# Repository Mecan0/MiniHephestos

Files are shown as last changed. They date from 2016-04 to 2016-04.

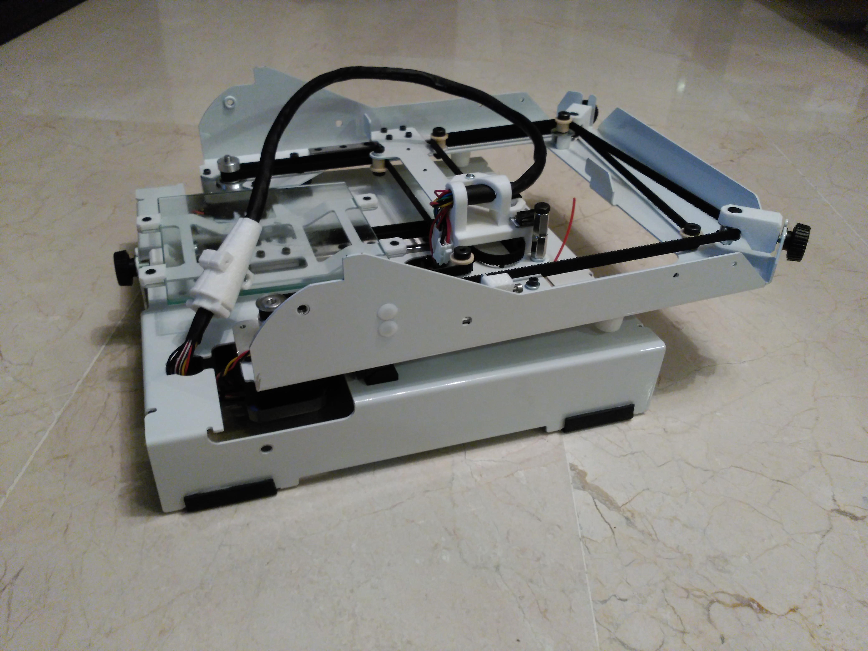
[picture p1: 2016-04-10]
03 The Hephestos Mini Printer.jpg

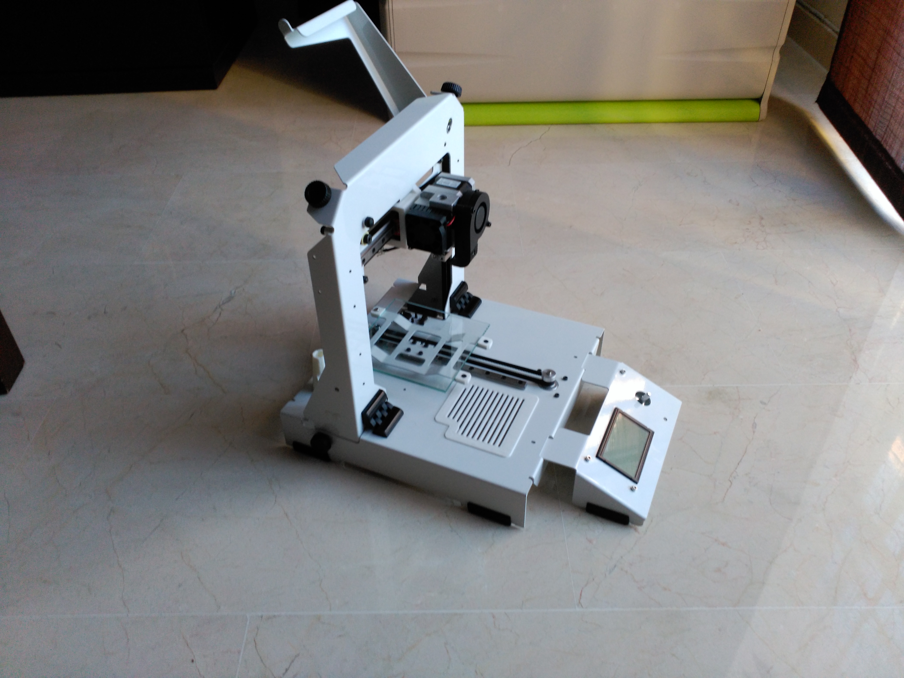
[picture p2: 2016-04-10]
02 The Hephestos Mini Printer.jpg

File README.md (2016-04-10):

# Hephestos-Mini
Mini 3D printer foldable

La Hephestos Mini nace como una colaboración entre BQ y Manuel Palacios para crear una impresora pequeña y transportable de fácil montaje.
El diseño está pensado para fabricarlo con chapa cortada por laser y posteriormente plegada.
Se ha tratado de minimizar el número de piezas diferentes para simplificar el montaje al máximo.
Los materiales utilizados para el diseño han sido los que integra BQ en sus impresoras, electrónica, extrusor, finales de carrera... 
Aunque es fácil modificarlo para adaptarlo a otros materiales.
El firmware elegido es de Repetier porque tiene un módulo para Core XZ, en Marlin existen otras versiones pero no están tan depurados.

Siente te libre de usar, modificar o adaptarlo a tu gusto.

A pioner in Core XZ printers is Nicholas Seward, Thanks a lot

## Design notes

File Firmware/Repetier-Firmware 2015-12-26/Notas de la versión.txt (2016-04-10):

Este firmware está basado en la versión 0.92.3

Tiene la corrección de Repetier que se muestra en el foro siguiente hecha maualmente

http://forums.reprap.org/read.php?267,392590,page=2 

Aunque a partir de la versión 0.92.6 esta corrección venía de serie.

Para funcionar con la Zum Mega 3D
En el archivo pins.h tiene cambiado:

#define ORIG_Z_ENABLE_PIN       77 //62

#define ORIG_FAN_PIN            12 //9
#define ORIG_PS_ON_PIN          81 //12

#define HEATER_0_PIN       9 //10
#define HEATER_1_PIN       10 //8
#define HEATER_2_PIN       8 //9

Una vez que se mete el firmware es necesario cargar los valores de la EEprom importando el archivo
 EEpromParaImprimir.epr desde Repetier Host.
 
 1) Conectar la impresora
 
 2) Menu Configuración\Config firmware EEPROM -----> Import EEPROM

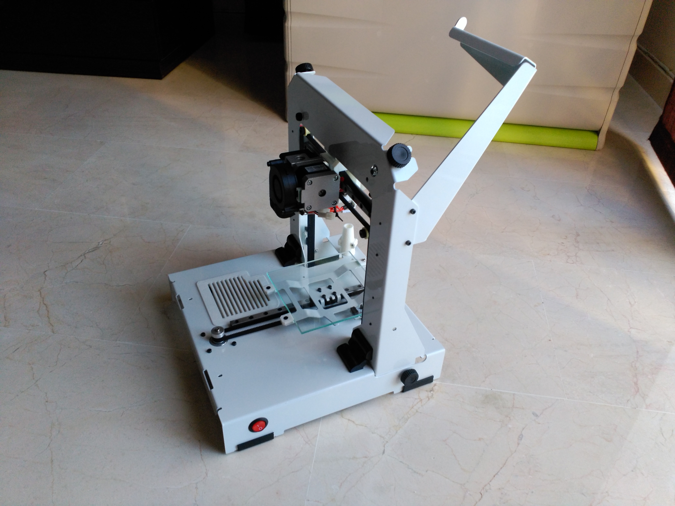
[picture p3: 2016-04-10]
Photos/2015-11-29 10.03.52.jpg

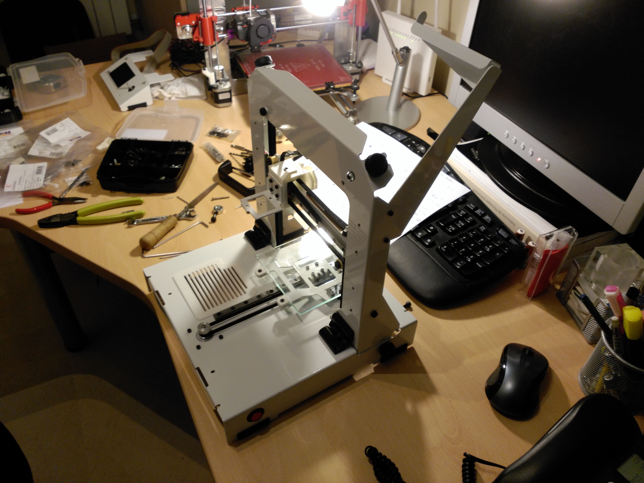
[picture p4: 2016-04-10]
Photos/2015-11-28 19.54.12.jpg

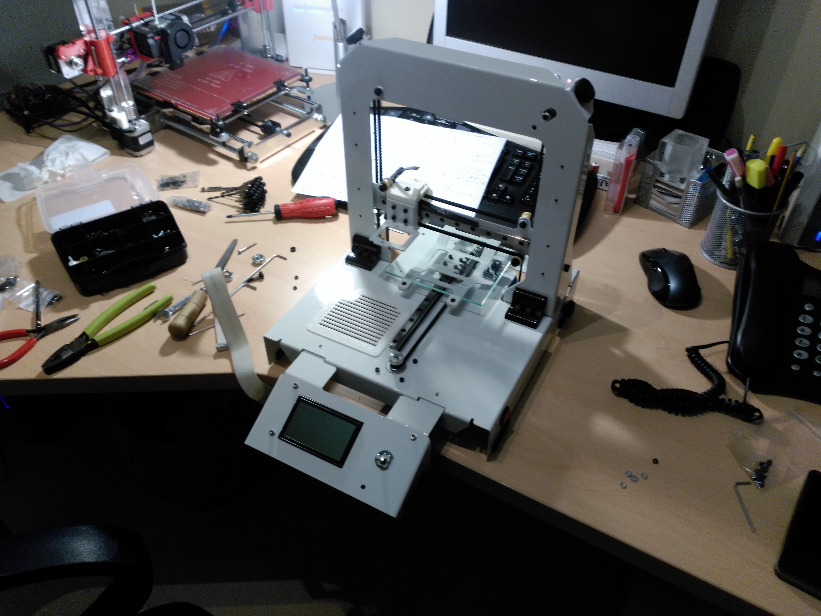
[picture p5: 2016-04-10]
Photos/2015-11-28 19.30.46.jpg

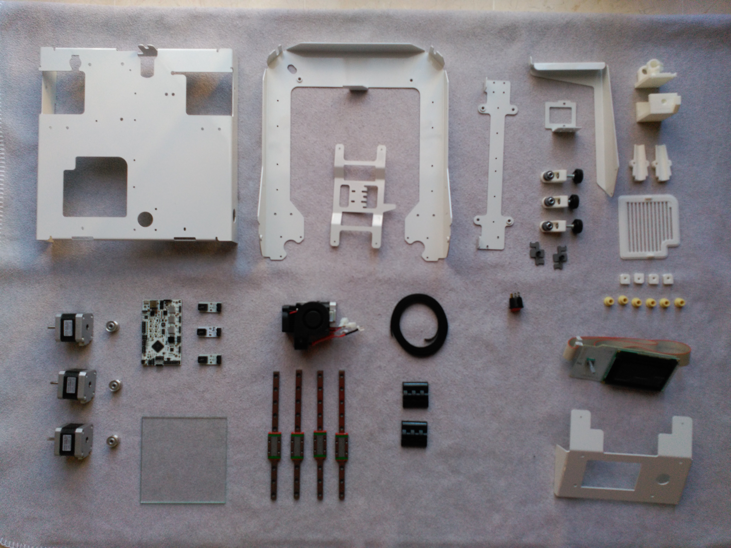
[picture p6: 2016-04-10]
04 Pieces.jpg

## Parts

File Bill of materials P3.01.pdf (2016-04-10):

REF | Nombre | Material | Unidades | Imagen

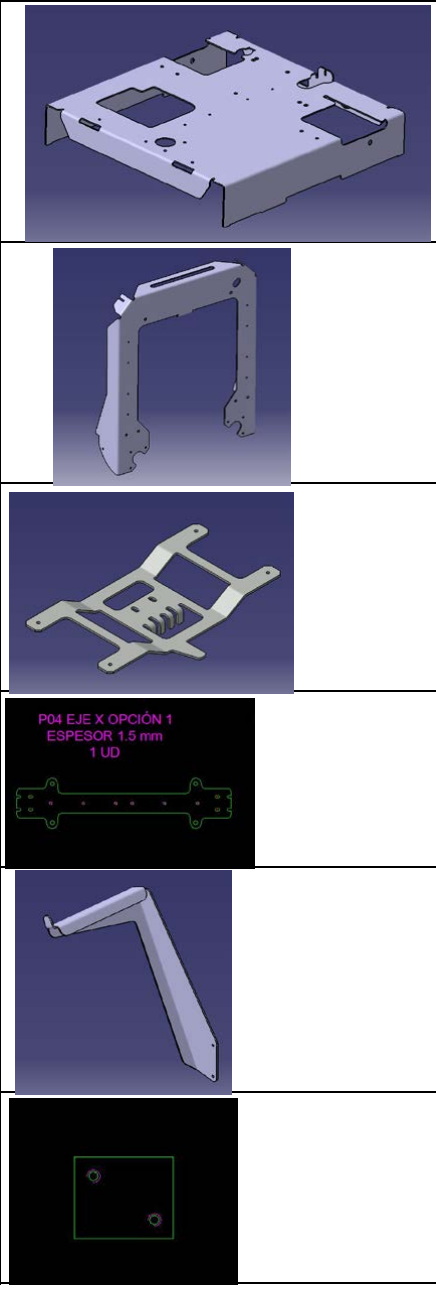
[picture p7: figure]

P01 | Base | | 1
P02 | Arco | | 1
P03 | Plataforma | | 1
P04 | Eje X | | 1
P05 | ReelH | | 1
P06 | FijCorrea | | 2

Metal

Metal

Metal

Metal

Metal

Metal

# BILL OF MATERIALS

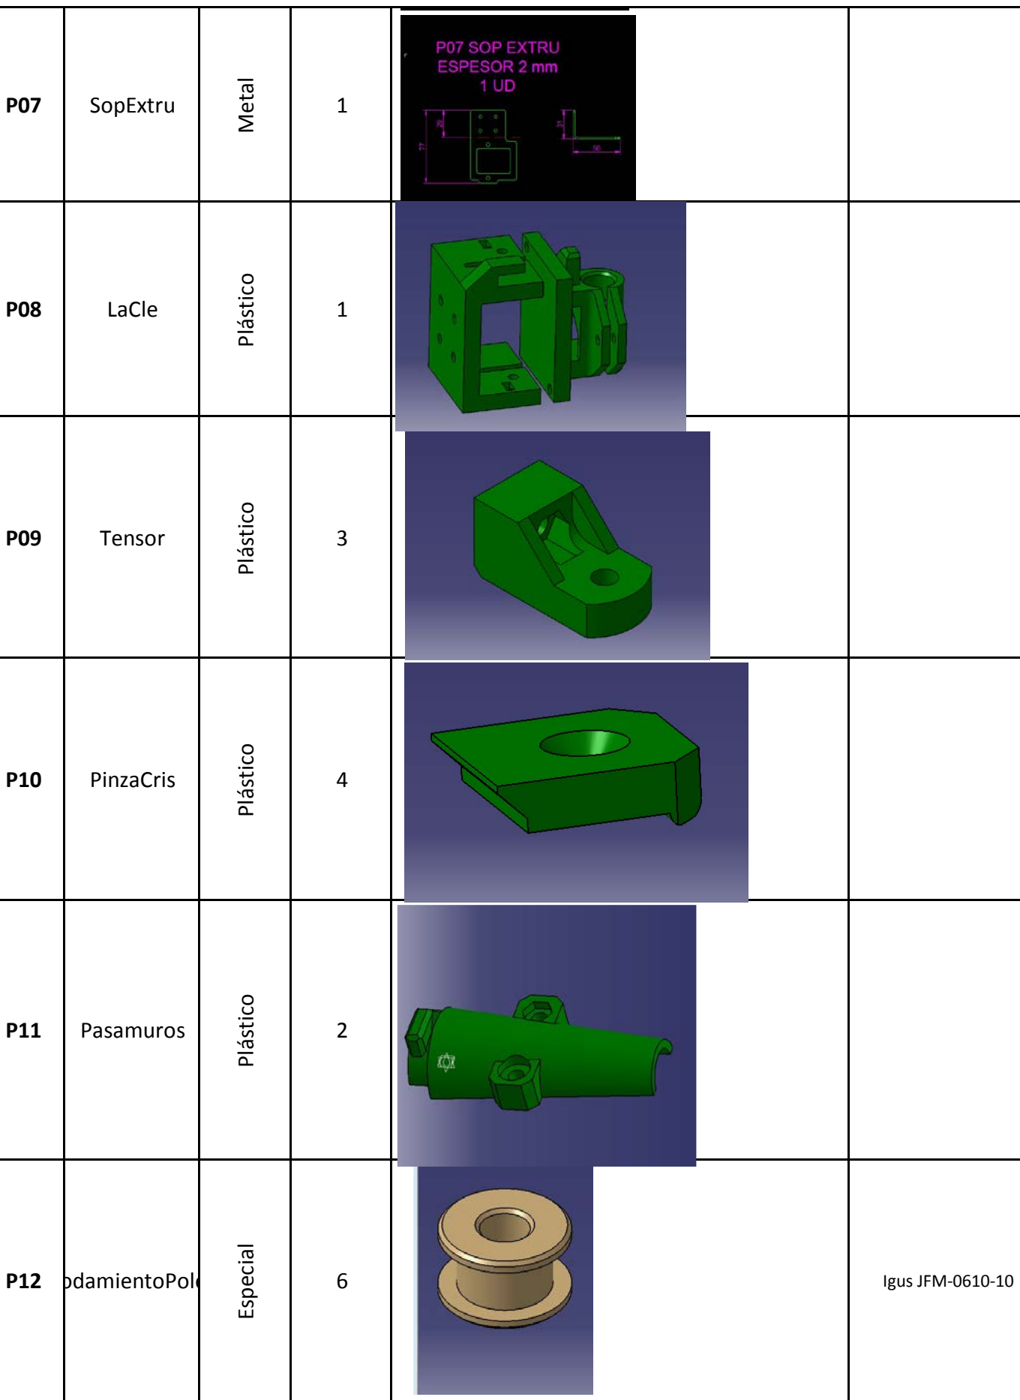
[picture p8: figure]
Metal; Plástico; P12 odamientoPole; Igus JFM-0610-10; Especial

P07 | SopExtru | 1
P08 | LaCle | 1
P09 | Tensor | 3
P10 | PinzaCris | 4
P11 | Pasamuros | 2

P13 | Rejilla | 1

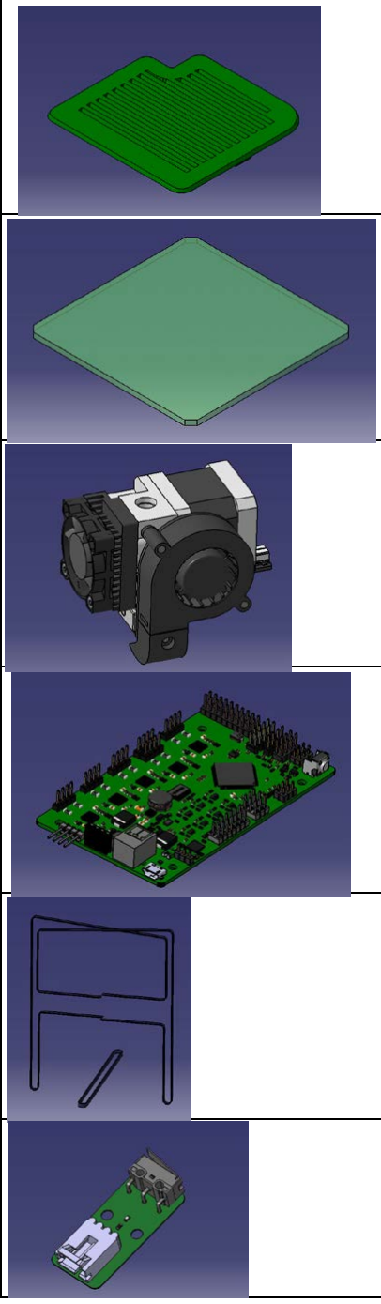
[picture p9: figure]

P14 | Cristal | 1 | Dimensiones 130 x 130 x 4 , perímetro biselado 1 x 45º
P15 | Extrusor | 1
P16 | Electrónica | 1
P17 | Correas | 1 | Correa eje Y 550 mm, Correas XZ 2 ud a 980 para después recortar
P18 | Fcarrera | 3

## Plástico

## Especial

## Comercial

## Comercial

## Comercial

## Comercial

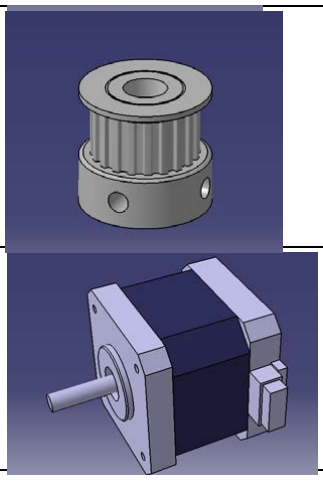
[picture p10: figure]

P19 | PoleaGT2 | 3
P20 | Motores | 3
P21 | 685ZZ | 3 | Rodamiento diam ext 11 mm, eje 5 mm y anchura 5 mm.
P22 | Bisagra | 2

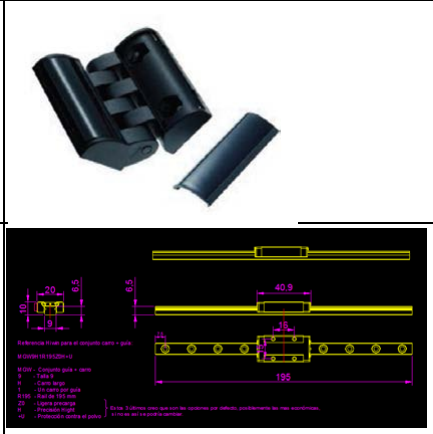
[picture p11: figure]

P23 | G_HIWIN | 4 | | Referencia Hiwin para el conjunto carro + guía: MGN9H1R195Z0H+U MGN - Serie MGN 9 - Talla 9 H - Carro largo 1 - Un carro por guía R195 - Rail de 195 mm Z0 - Ligera precarga H - Precisión Hight +U - Protección contra el polvo

## Comercial

## Comercial

## Comercial

## Comercial

## Comercial

## OPCIONAL

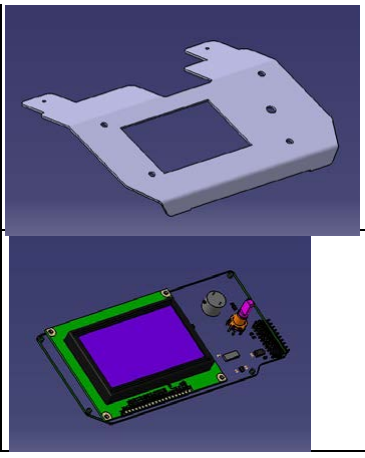
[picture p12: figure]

## P30 SopLCD

## Metálico

1

## P31 LCD

## Comercial

1

Tornillería | | Para: | Cantidad
Tornillo DIN912 M3x5 | Cabeza Allen | Para motores | 9 ud
Tornillo DIN912 M3x5 | Cabeza Allen | Para fijar guías y rollo y caros Z | 25 ud
Tornillo DIN912 M4x8 | Cabeza Allen | Para Bisagras y cogida correas | 10 ud
Tornillo DIN7379 M5x6x12 | Cabeza Allen | Tornillos tope guía | 6 ud | Longitud parte diam 6
Tuercas M4 DIN934 | | Dentro bisagras | 8 ud
Tuercas M5 DIN934 | | Tensores y Calzo Correa | 7 ud
Tuercas M5 autoblocantes | | Tensores | 3 ud
Arandelas DIN125 M4 estandar | | Bisagras | 8 ud | No las usé
Arandelas DIN125 M5 estándar | | Tensores | 9 ud
Arandelas DIN9021 M5 vuelo | | Tensores | 6 ud
Tornillo DIN933 M5x20 | Cabeza hexagonal | Tensores y final de carrera X | 4 ud
Tornillo DIN912 M3x20 | Cabeza Allen | Tope FCZ | 1 ud
Tuercas M3 DIN 934 | Cabeza Allen | Tope final de Carrera Z y carros Z | 9 ud
Tuerca larga de M5 DIN6334 | | Tope final de carrera X | 2 ud
Tuerca M10 Din 934 | | Suplemento polea | 2 ud
Tornillo DIN 912 M3x5 | Cabeza Allen | Union Plataf-carro y EjeX-Carro | 12 ud
Tornillo DIN 945 M3x8 | Cabeza cónica Allen | Pinzas Cristal | 4 ud
Tornillo DIN 912 M3x10 | Cabeza Allen | fijac electrónica, Carros Z | 8 ud
Tornillo DIN 912 M3x12 | Cabeza Allen | Union SopExtr-Carro | 4 ud
Tornillo para plástico 3x10 | Wurth Ref: 42 16 3 10 | Tapa Cle, Pasamuros y Fijación Cable | 6 ud
Tornillo apriete manual M5x10 | Essentra Ref: KTSR-23M05M10 Fijación a 90º | 2 ud | Lo ideal sería que tubi
http://www.essentracomponents.es/pomos-de-agarre-344390
Tornillo aprete manual M5x20 | Essentra Ref: KTSR-23M05M20 Tensores | 3 ud | En Essentra tienen de
| Ver también Essentra Ref.: 466347

Essentra

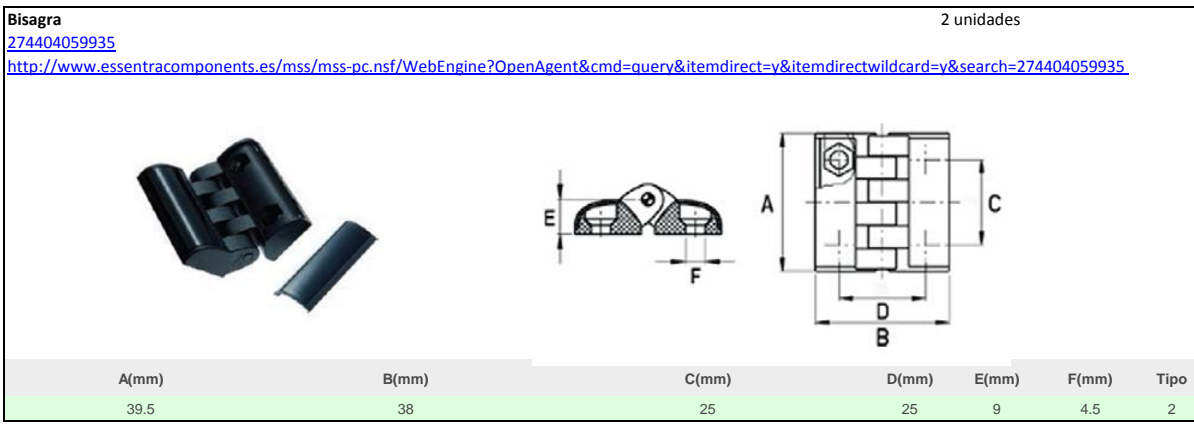
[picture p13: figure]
Bisagra; 2 unidades; 274404059935 http://www.essentracomponents.es/mss/mss-pc.nsf/WebEngine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; Tipo

Cantidad nec.

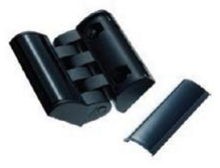
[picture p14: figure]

Separador electrónica, finales de carrera.
RLCBSR-5-01BK (http://www.essentracomponents.es/mss/mss-pc.nsf/WebEngine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) | Para final de carrera Z | Altura de parada 7,9 mm | 5 | Ver cogida LCD
RLCBSPR-4-01 (http://www.essentracomponents.es/mss/mss-pc.nsf/WebEngine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) | Para final de carrera Y | Altura de parada 6,4 | 2
http://www.essentracomponents.es/separador-circuito-impreso-con-base-de-remache---rlcbsrrlcbsrerlcbsprrcbsr
Esta referencia es en color negro, también existe en blanco. Tipo 1 Con Gancho.


Patas | RG-1 | 4 ud x 50mm
http://www.essentracomponents.es/mss/mss-pc.nsf/WebEngine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


Otra opción para las patas mas económica pero mucho mas fea: 492988S

http://www.essentracomponents.es/protector-de-bordes-de-pvc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


4 ud x 50mm
| Dependerá del precio y de las muestras

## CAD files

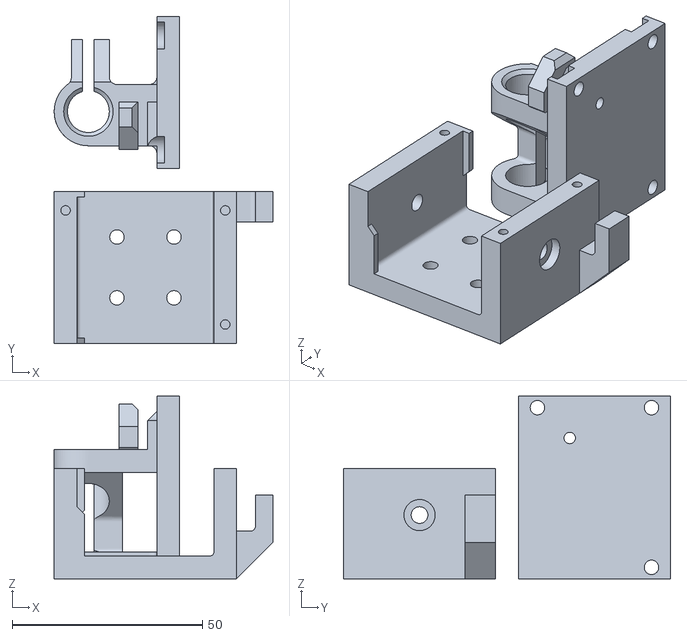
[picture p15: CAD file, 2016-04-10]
STL Files/P08_LaCle.stl
57.5 x 86.0 x 48.0

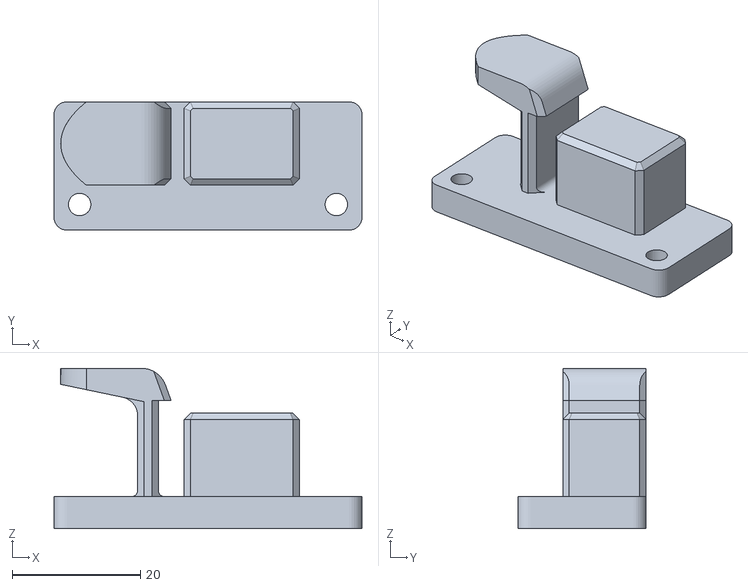
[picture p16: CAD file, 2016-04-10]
STL Files/P23_Cierre.stl
48.0 x 20.0 x 25.0

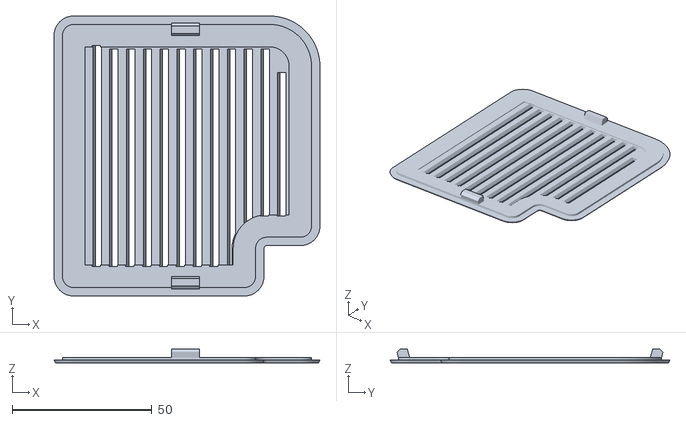
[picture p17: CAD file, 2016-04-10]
STL Files/P13_Rejilla.stl
95.0 x 100.0 x 5.00

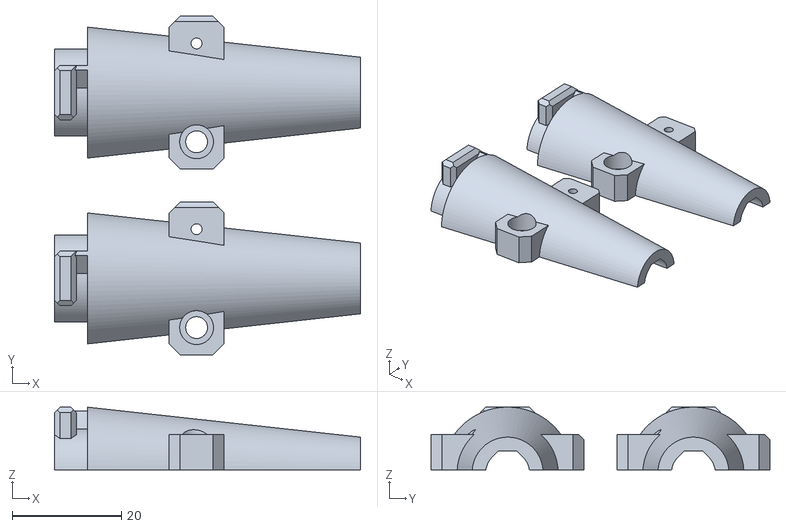
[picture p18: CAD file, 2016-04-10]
STL Files/P11_Pasamuros.stl
56.0 x 62.0 x 11.5

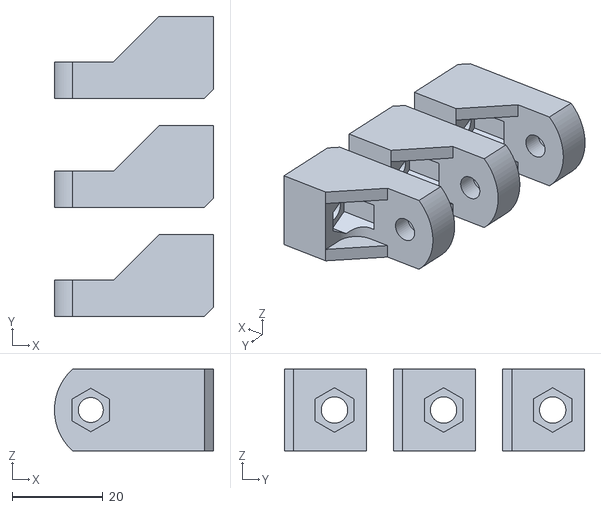
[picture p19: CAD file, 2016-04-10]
STL Files/P09_TensorV3.stl
35.0 x 66.0 x 18.0

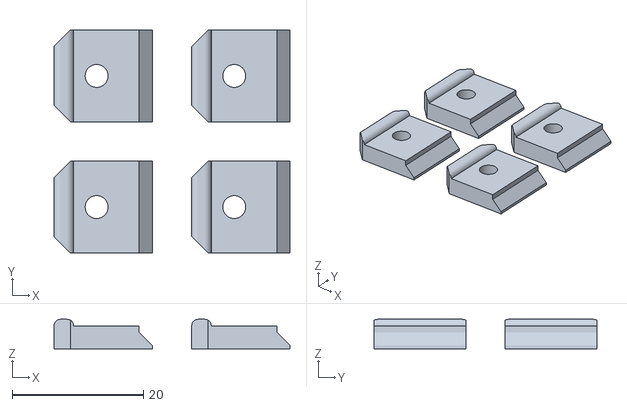
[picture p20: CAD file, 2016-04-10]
STL Files/P10_PinzaCris.stl
36.0 x 34.0 x 4.50

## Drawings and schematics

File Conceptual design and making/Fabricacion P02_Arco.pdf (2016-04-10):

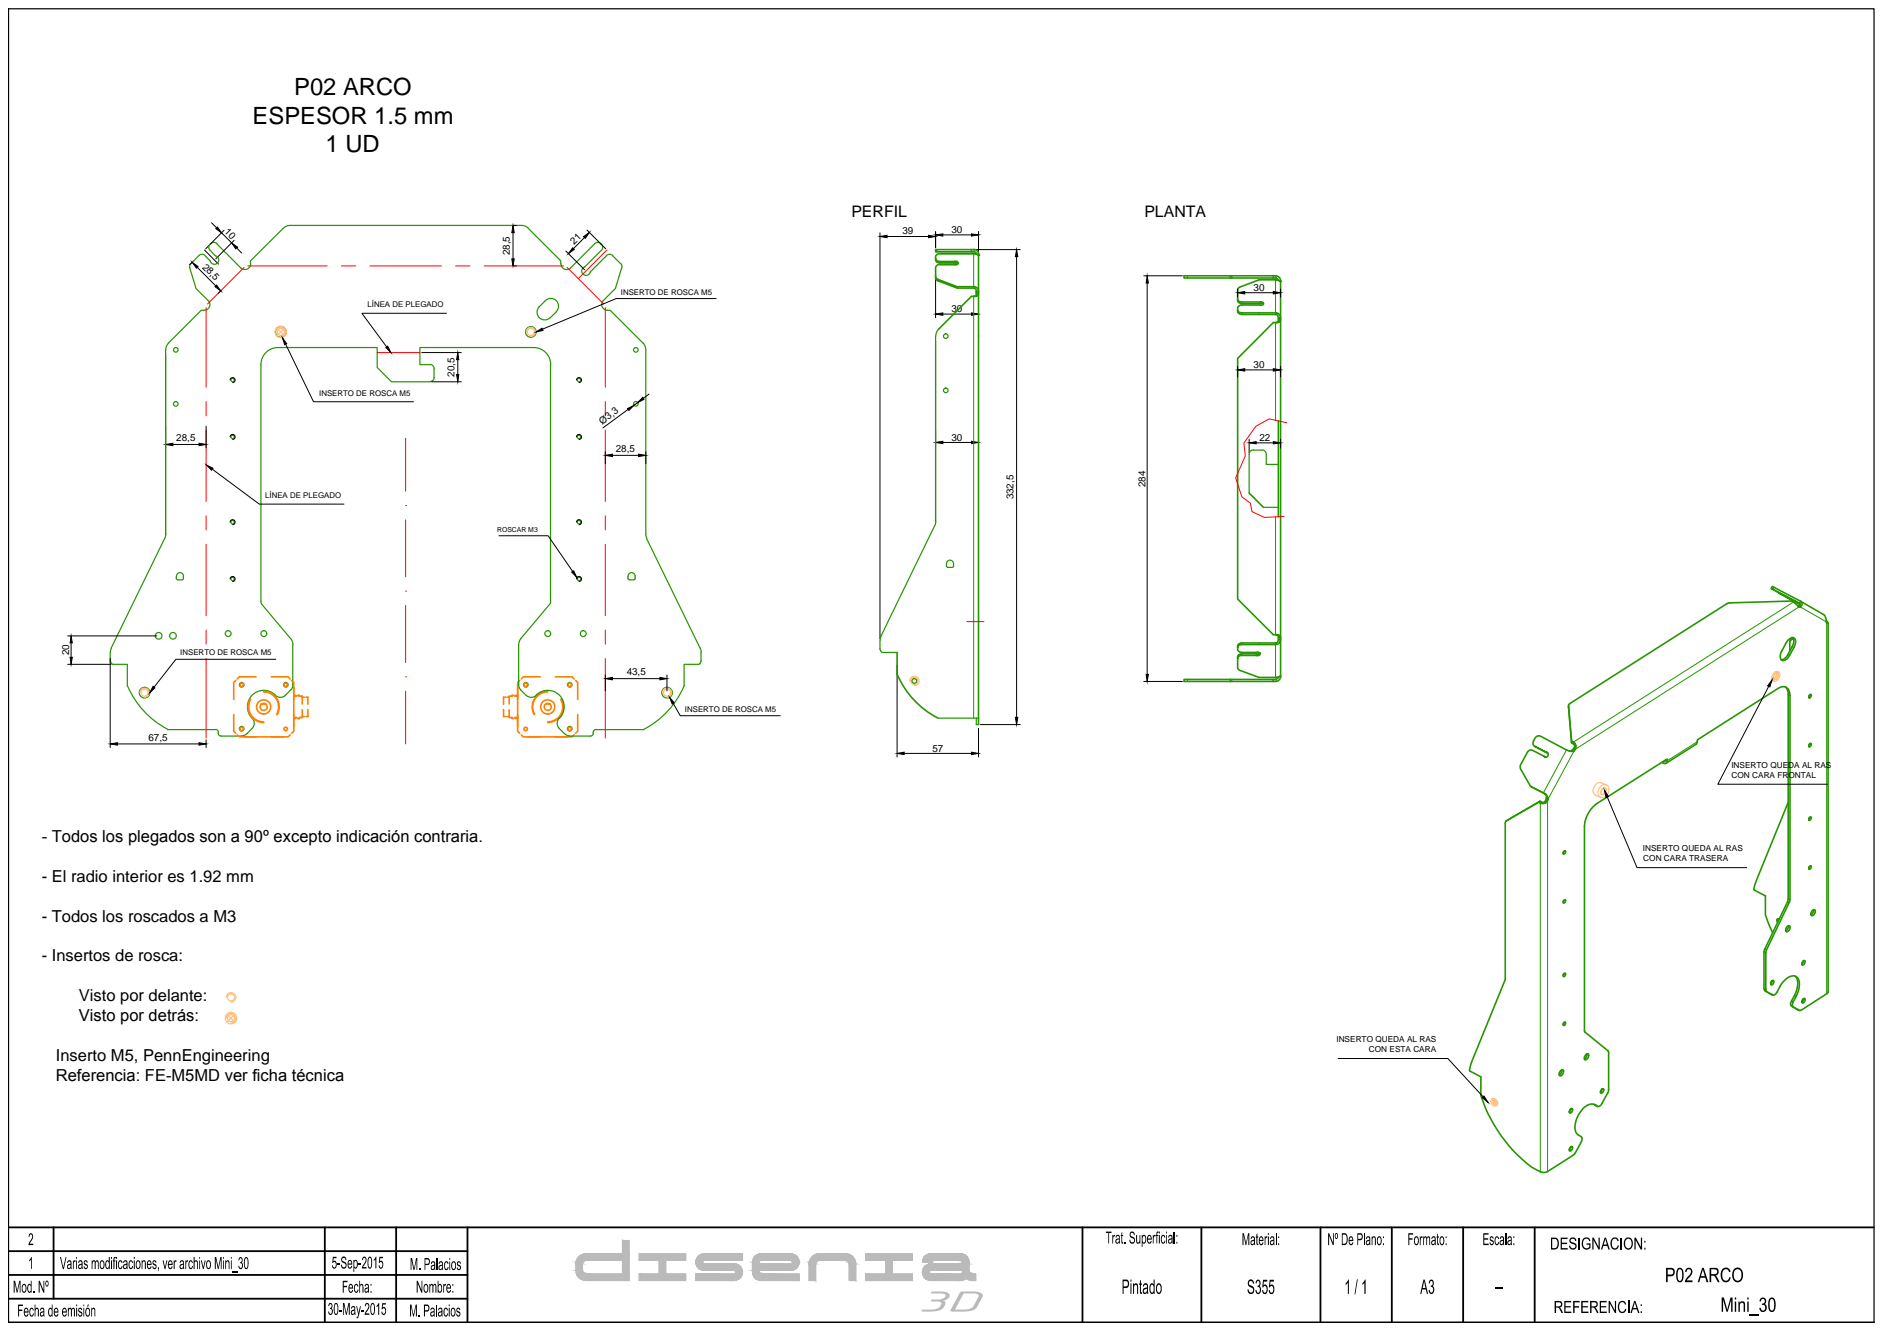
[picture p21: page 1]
P02 ARCO ESPESOR 1.5 mm 1 UD; ROSCAR M3

INSERTO DE ROSCA M5

INSERTO QUEDA AL RAS CON CARA FRONTAL

7RGRVORVSOHJDGRVVRQDH[FHSWRLQGLFDFLyQFRQWUDULD

INSERTO QUEDA AL RAS CON CARA TRASERA

- El radio interior es 1.92 mm

- Todos los roscados a M3

- Insertos de rosca:

Visto por delante:
9LVWRSRUGHWUiV

INSERTO QUEDA AL RAS CON ESTA CARA

Inserto M5, PennEngineering
5HIHUHQFLD)(00'YHUILFKDWpFQLFD

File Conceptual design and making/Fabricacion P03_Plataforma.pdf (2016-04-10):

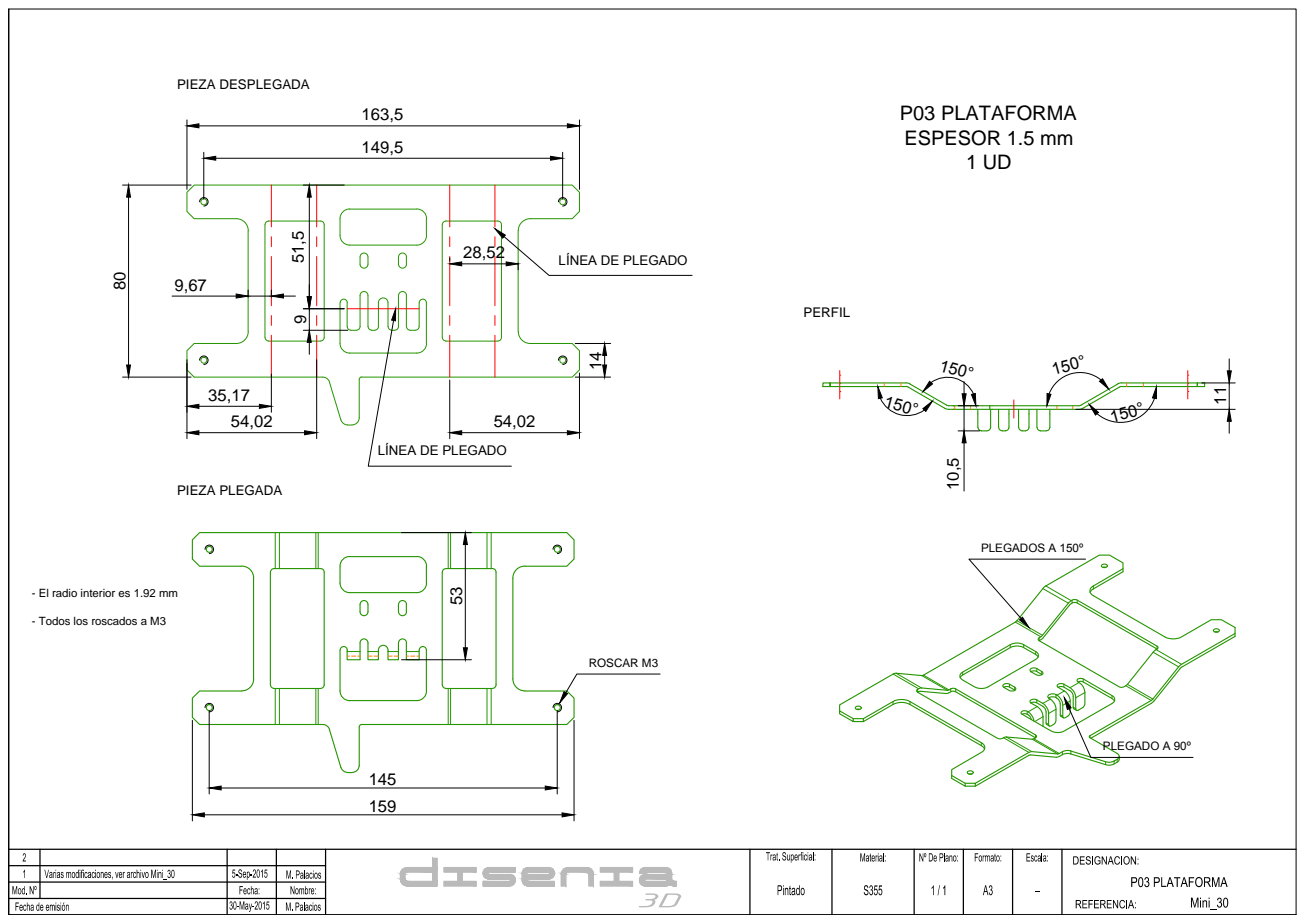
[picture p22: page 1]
P03 PLATAFORMA ESPESOR 1.5 mm 1 UD; PIEZA DESPLEGADA; PIEZA PLEGADA; ROSCAR M3

- El radio interior es 1.92 mm

- Todos los roscados a M3

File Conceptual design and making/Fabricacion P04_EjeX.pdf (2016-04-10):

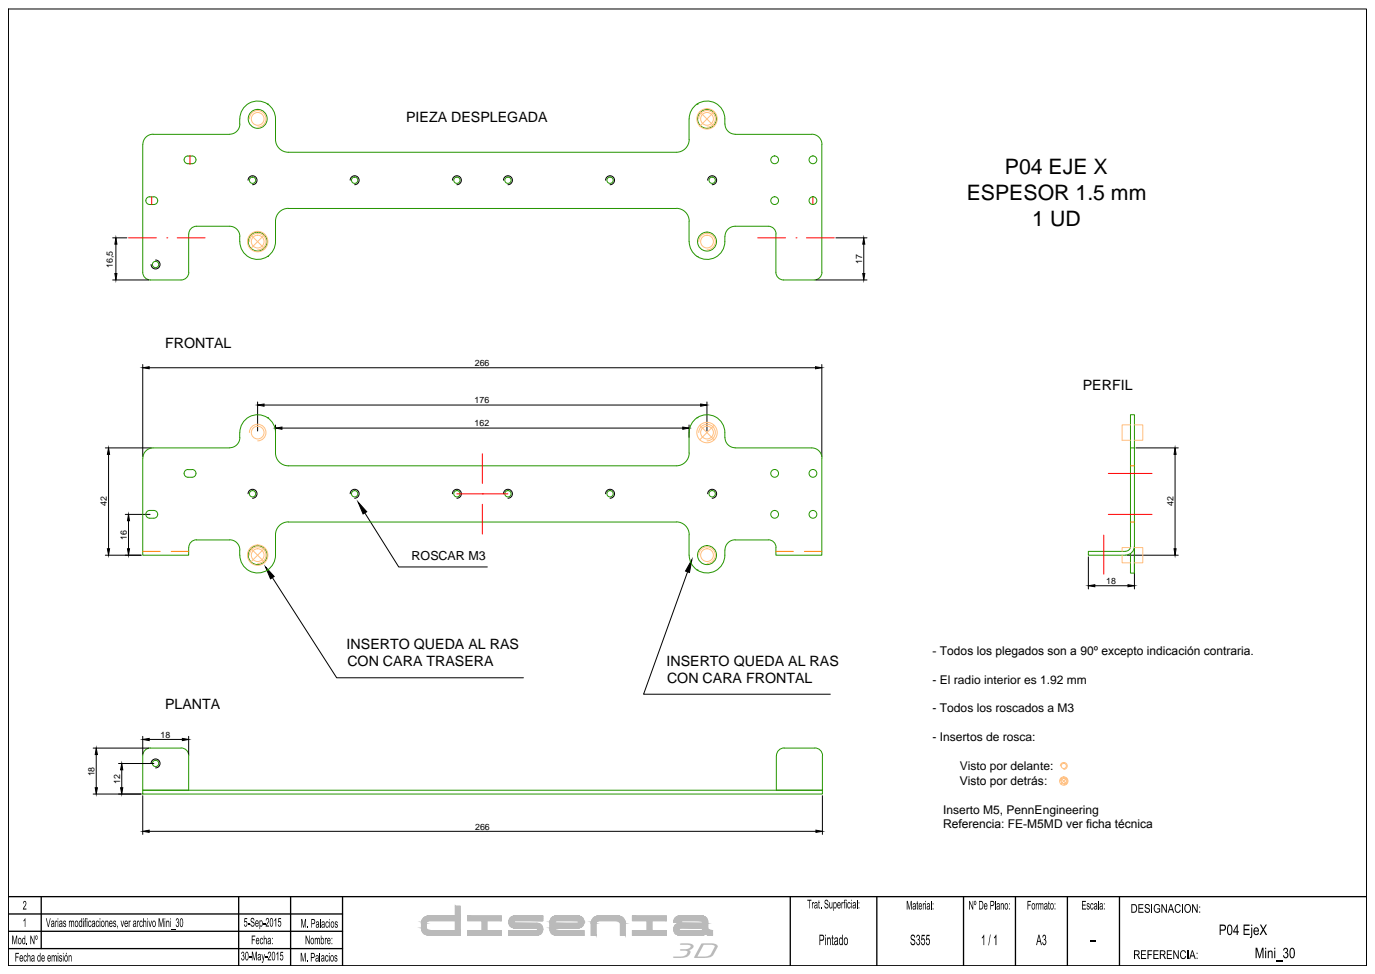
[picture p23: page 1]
P04 EJE X ESPESOR 1.5 mm 1 UD; ROSCAR M3; PIEZA DESPLEGADA

INSERTO QUEDA AL RAS
CON CARA TRASERA

7RGRVORVSOHJDGRVVRQDH[FHSWRLQGLFDFLyQFRQWUDULD

CON CARA FRONTAL

- El radio interior es 1.92 mm

- Todos los roscados a M3

- Insertos de rosca:

Visto por delante:
9LVWRSRUGHWUiV

Inserto M5, PennEngineering
5HIHUHQFLD)(00'YHUILFKDWpFQLFD

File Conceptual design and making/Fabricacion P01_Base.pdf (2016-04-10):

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

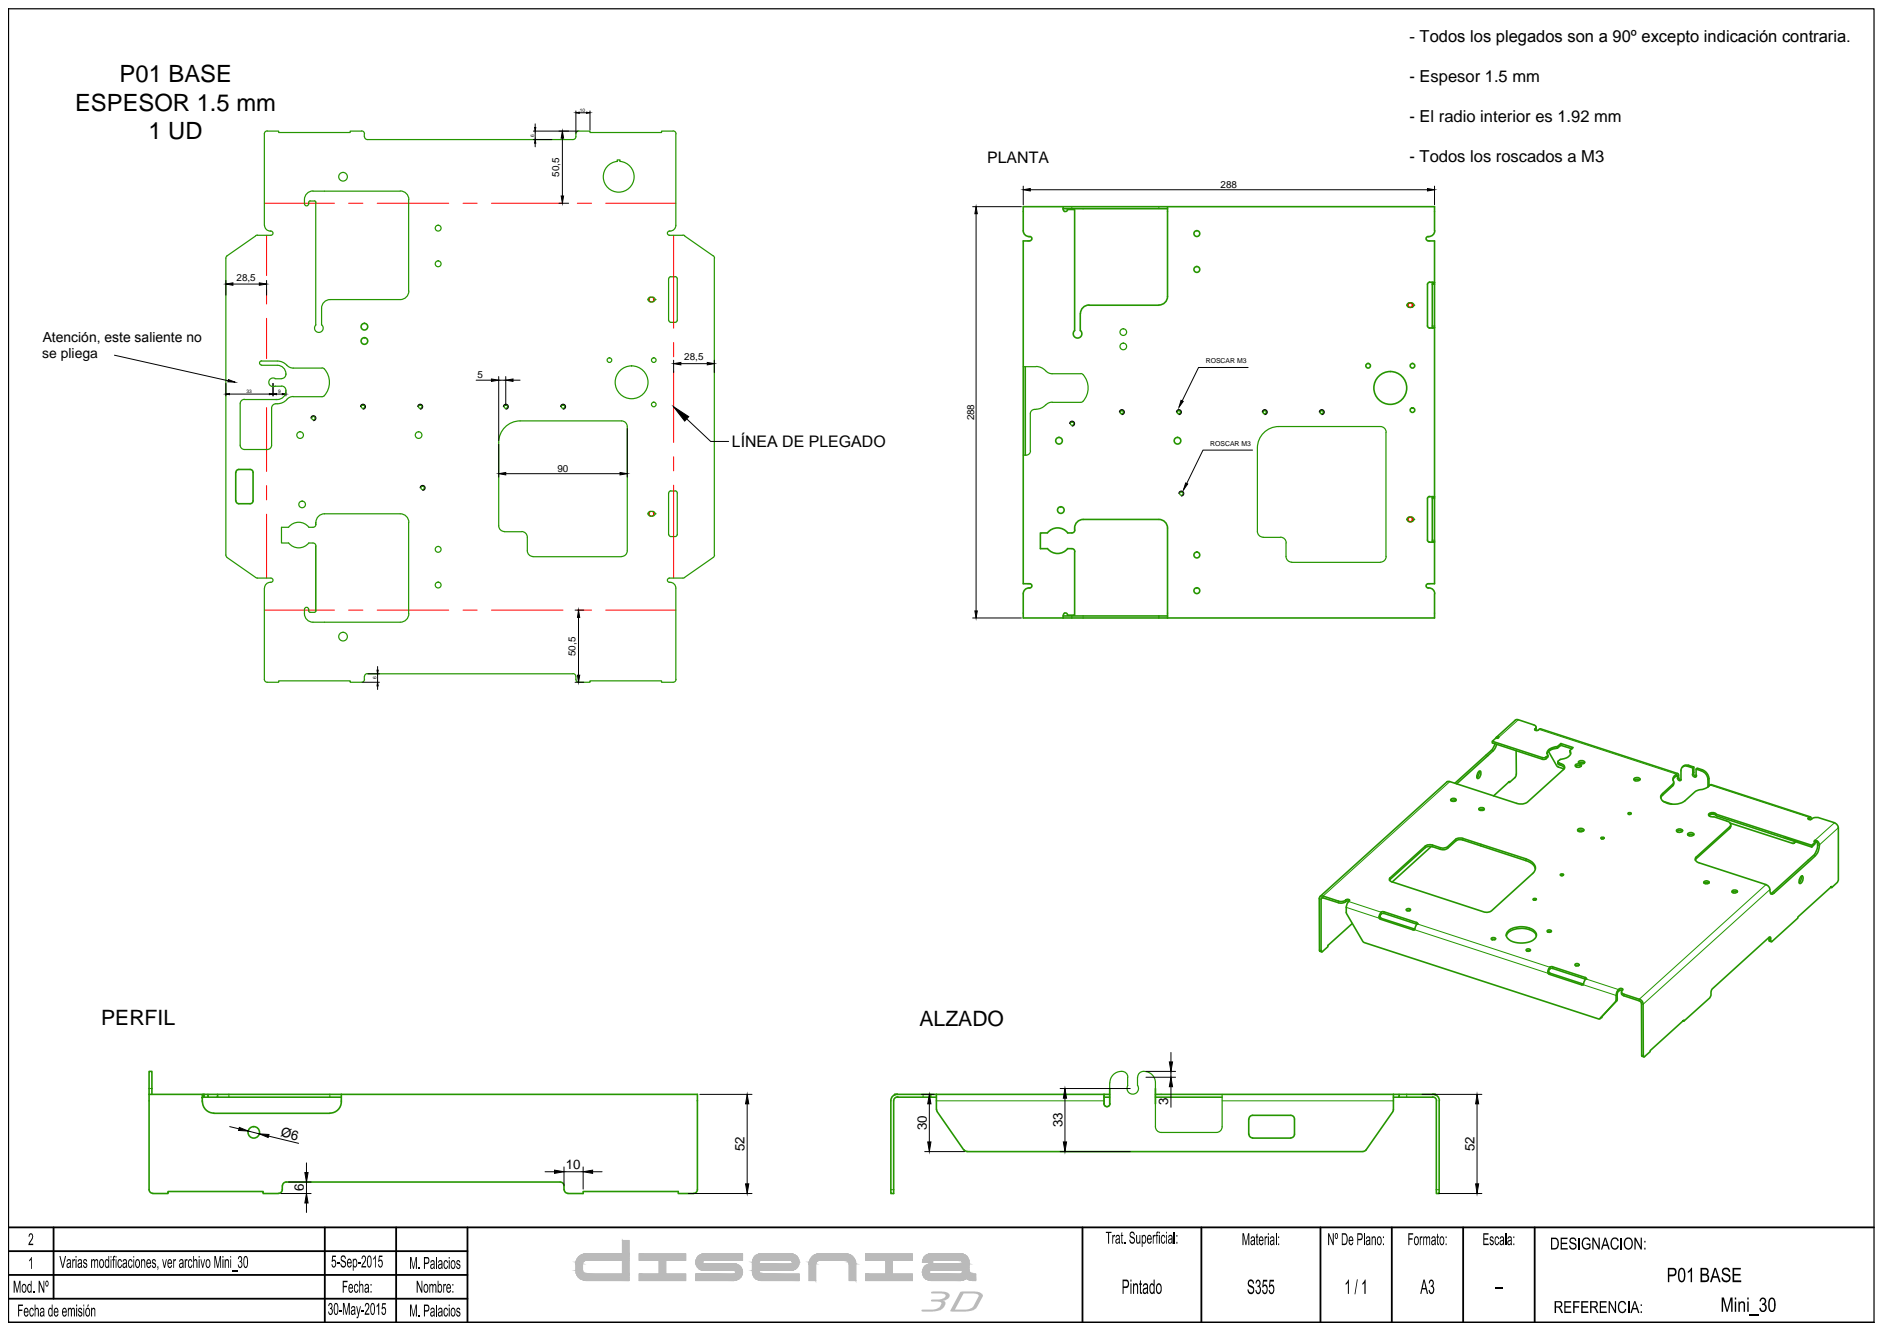
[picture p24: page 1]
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

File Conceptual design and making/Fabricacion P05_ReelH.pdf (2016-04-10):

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

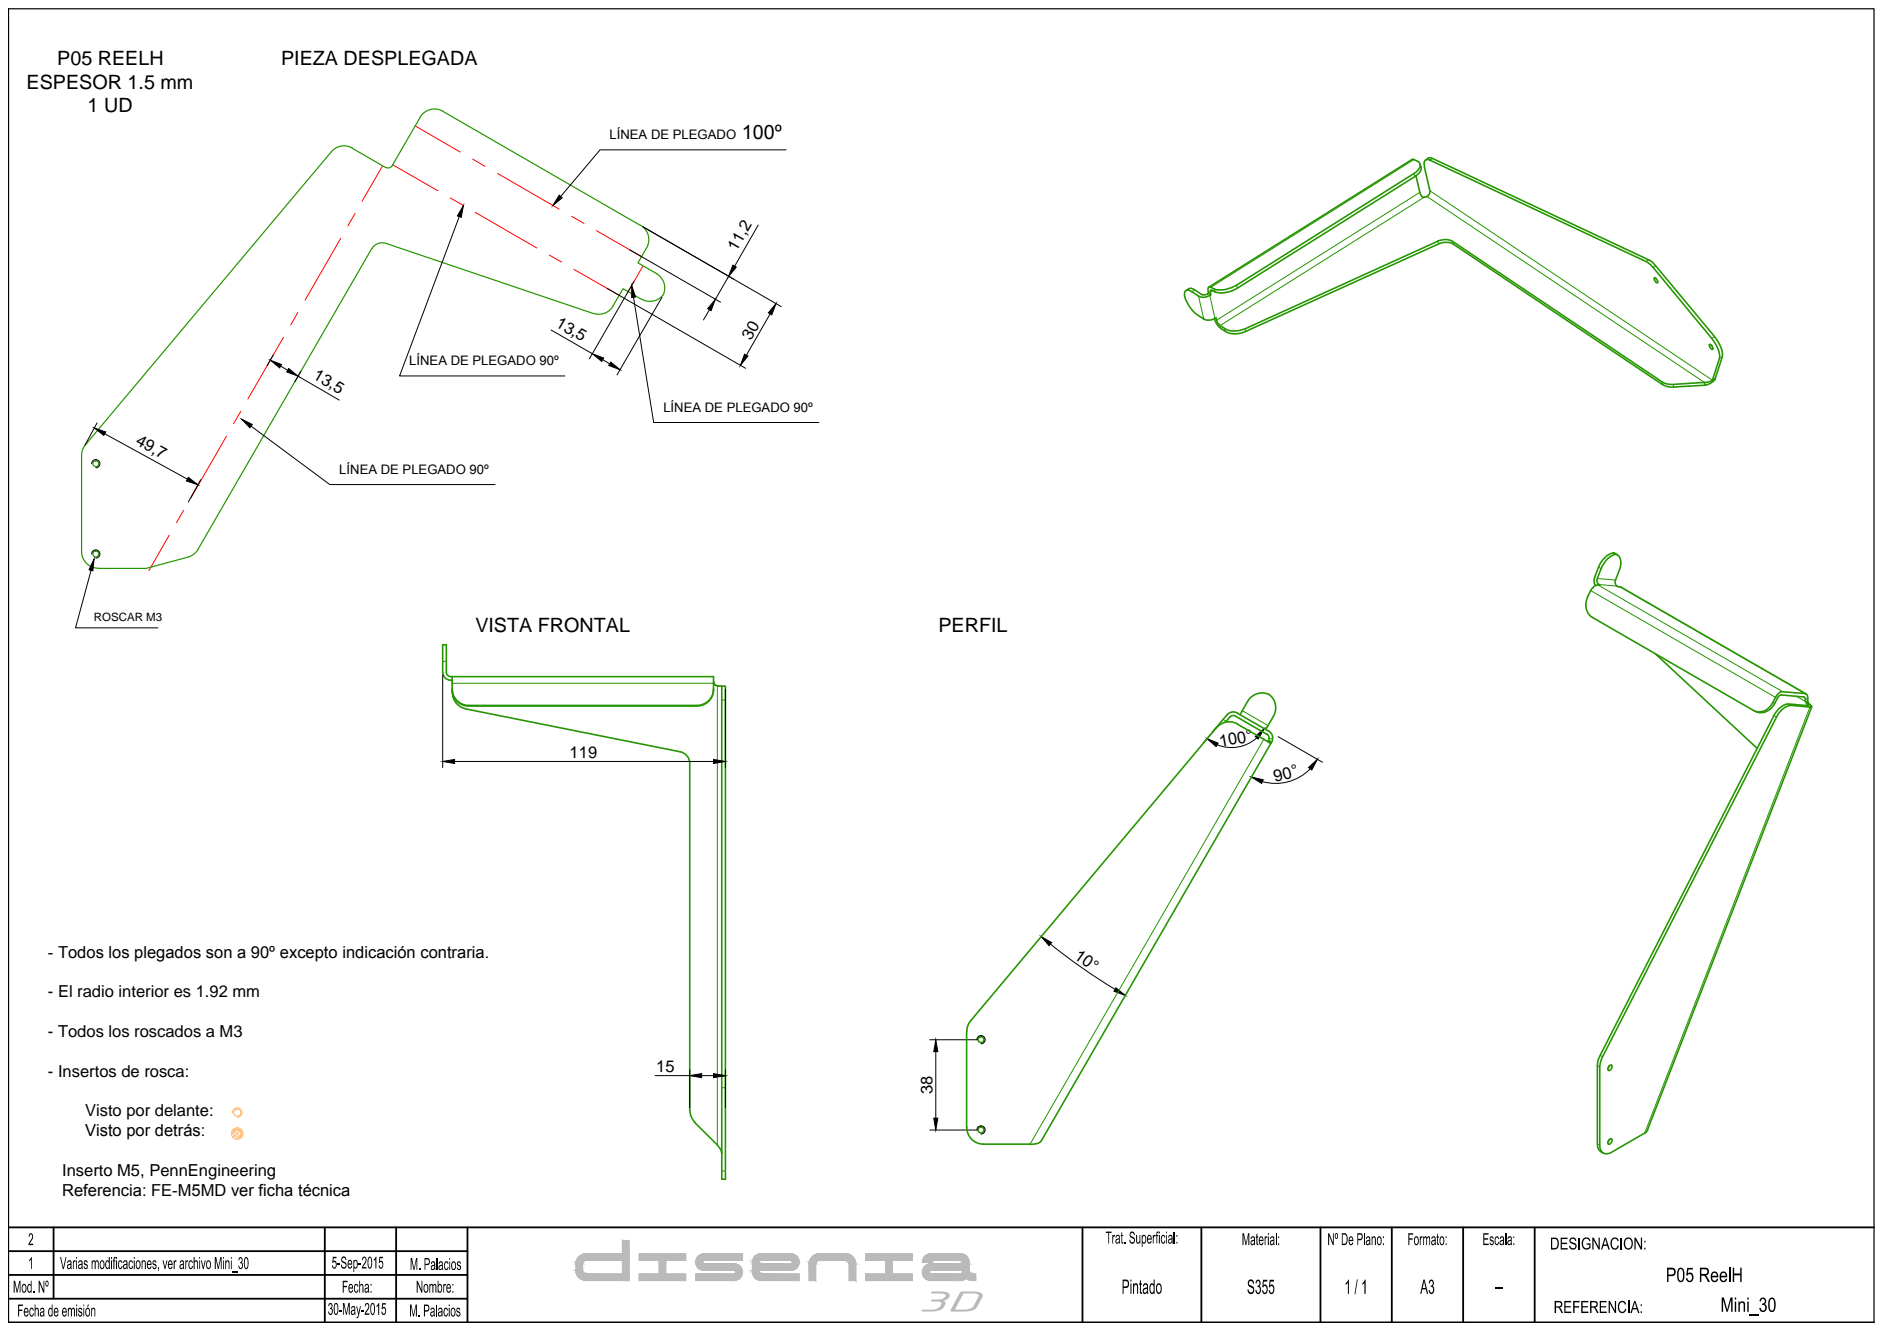
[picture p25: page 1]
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

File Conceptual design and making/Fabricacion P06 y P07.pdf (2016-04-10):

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

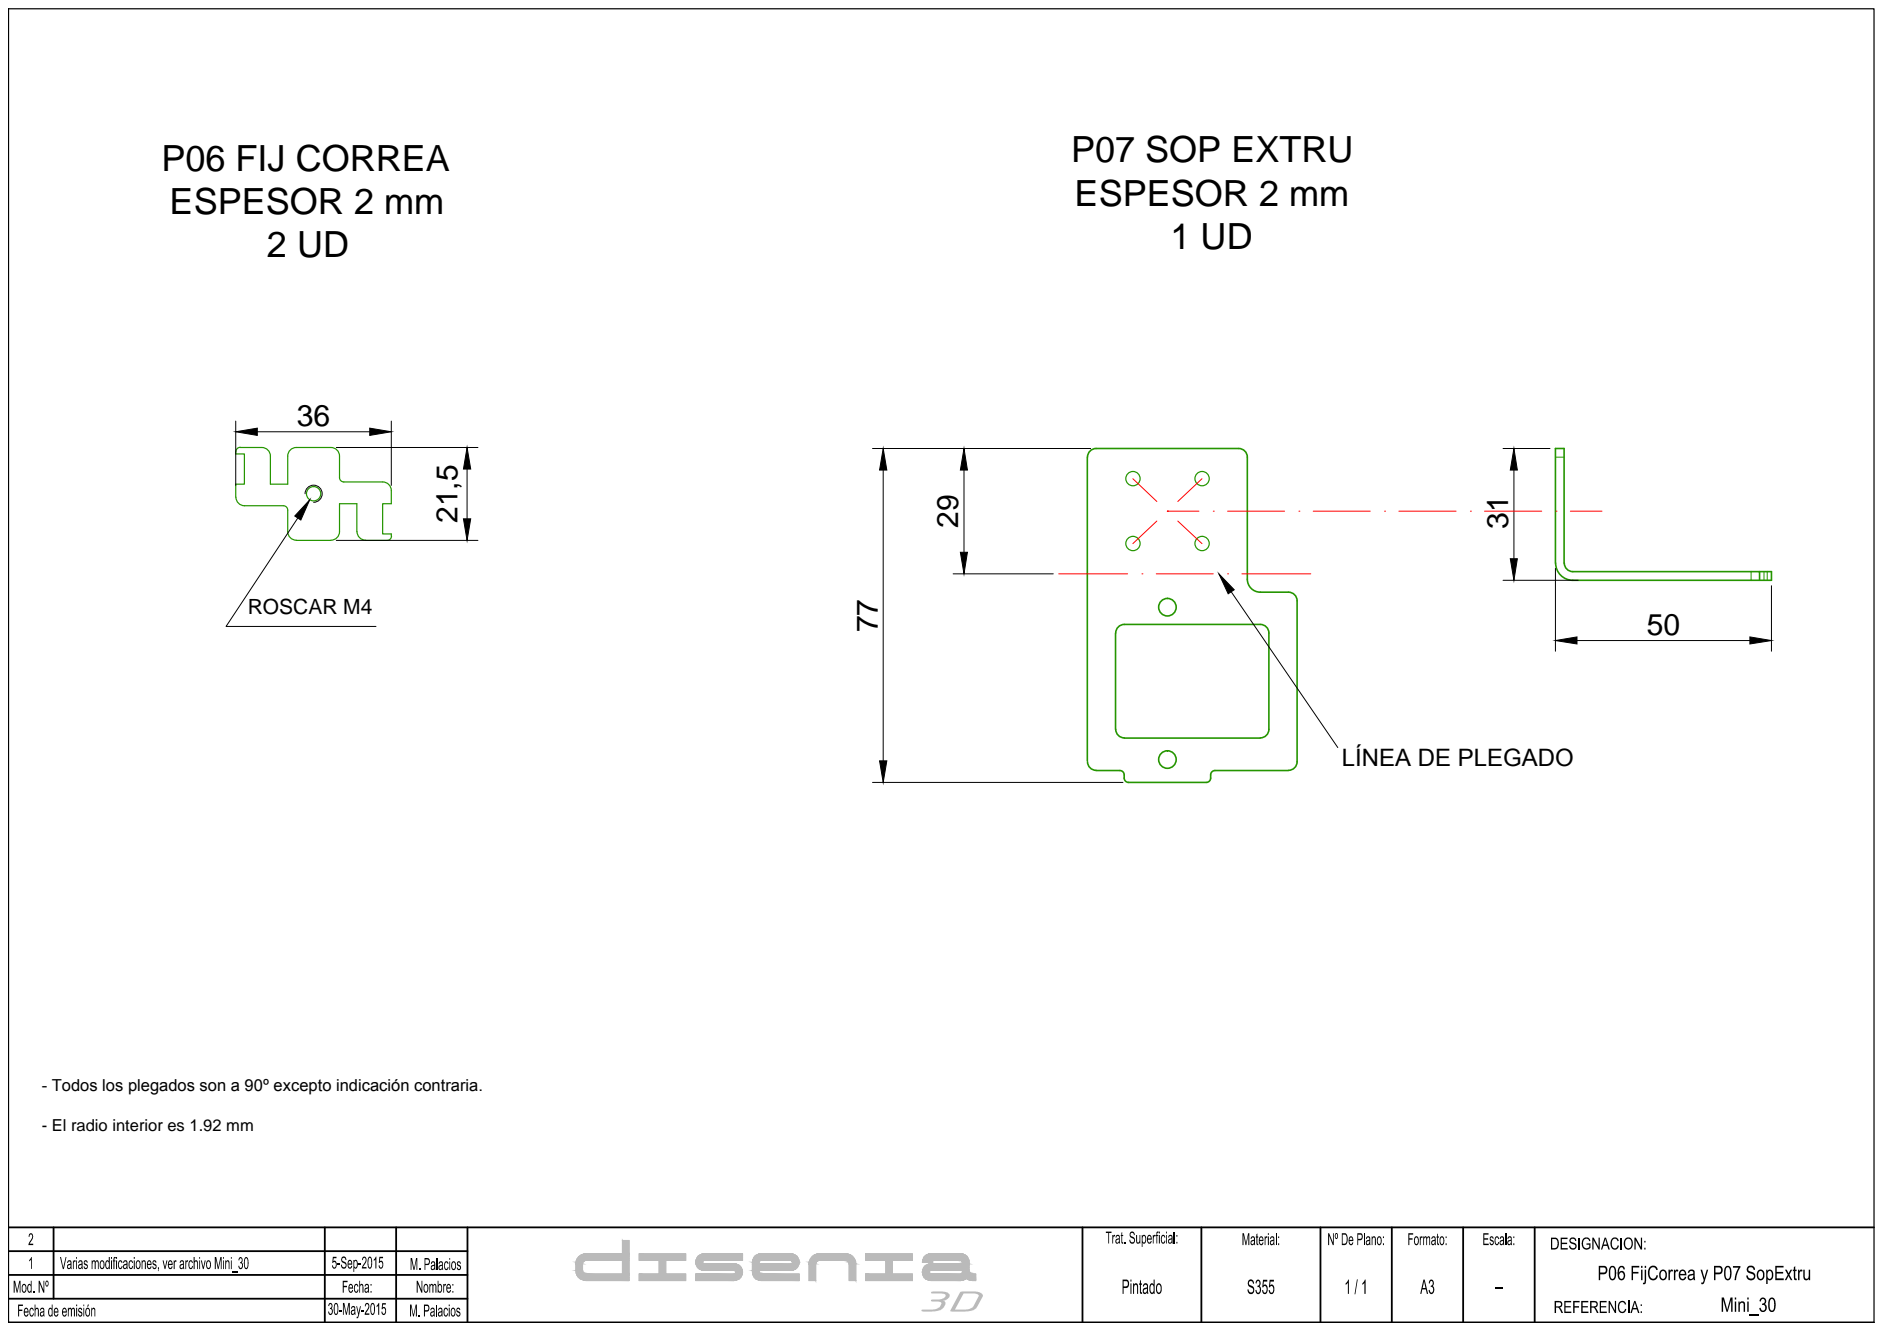
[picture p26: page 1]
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

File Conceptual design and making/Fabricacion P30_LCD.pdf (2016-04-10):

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

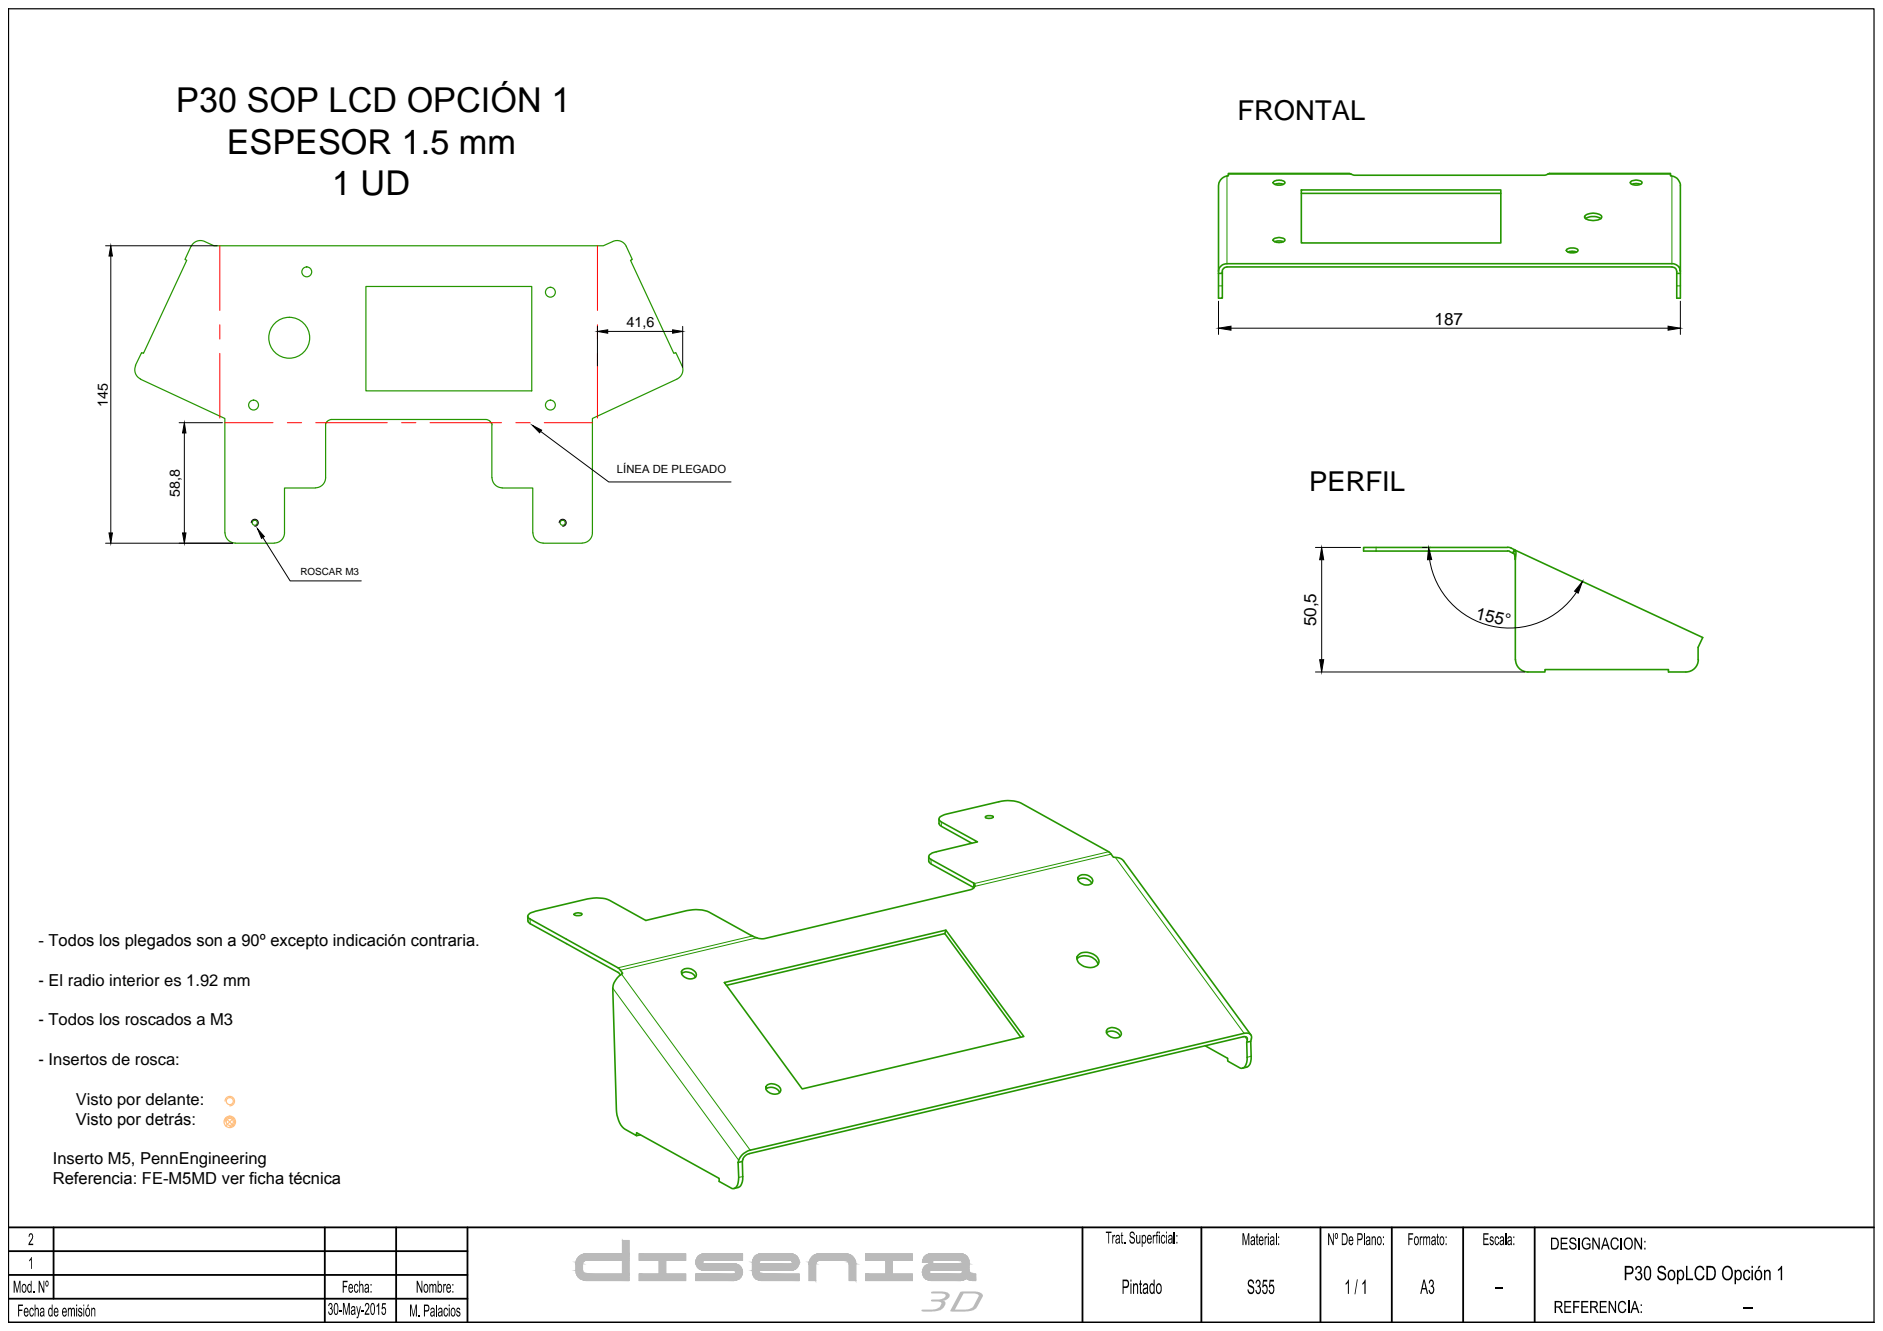
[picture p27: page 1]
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

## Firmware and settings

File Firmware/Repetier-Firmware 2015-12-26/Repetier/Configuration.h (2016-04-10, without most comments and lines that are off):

#define CONFIGURATION_H
#define NUM_EXTRUDER 1
#define MOTHERBOARD 33
#include "pins.h"
#define FAN_PIN 12
#define FAN_BOARD_PIN -1
#define BLUETOOTH_SERIAL  -1
#define BLUETOOTH_BAUD  115200
#define MIXING_EXTRUDER 0
#define DRIVE_SYSTEM 9
#define XAXIS_STEPS_PER_MM 320
#define YAXIS_STEPS_PER_MM 160
#define ZAXIS_STEPS_PER_MM 320
#define EXTRUDER_FAN_COOL_TEMP 50
#define PDM_FOR_EXTRUDER 1
#define PDM_FOR_COOLER 1
#define DECOUPLING_TEST_MAX_HOLD_VARIANCE 20
#define DECOUPLING_TEST_MIN_TEMP_RISE 1
#define KILL_IF_SENSOR_DEFECT 0
#define RETRACT_ON_PAUSE 2
#define PAUSE_START_COMMANDS ""
#define PAUSE_END_COMMANDS ""
#define EXT0_X_OFFSET 0
#define EXT0_Y_OFFSET 0
#define EXT0_Z_OFFSET 0
#define EXT0_STEPS_PER_MM 204
#define EXT0_TEMPSENSOR_TYPE 1
#define EXT0_TEMPSENSOR_PIN TEMP_0_PIN
#define EXT0_HEATER_PIN HEATER_0_PIN
#define EXT0_STEP_PIN ORIG_E0_STEP_PIN
#define EXT0_DIR_PIN ORIG_E0_DIR_PIN
#define EXT0_INVERSE 1
#define EXT0_ENABLE_PIN E0_ENABLE_PIN
#define EXT0_ENABLE_ON 0
#define EXT0_MAX_FEEDRATE 10
#define EXT0_MAX_START_FEEDRATE 20
#define EXT0_MAX_ACCELERATION 1000
#define EXT0_HEAT_MANAGER 3
#define EXT0_WATCHPERIOD 1
#define EXT0_PID_INTEGRAL_DRIVE_MAX 230
#define EXT0_PID_INTEGRAL_DRIVE_MIN 40
#define EXT0_PID_PGAIN_OR_DEAD_TIME 7
#define EXT0_PID_I 2
#define EXT0_PID_D 40
#define EXT0_PID_MAX 255
#define EXT0_ADVANCE_K 0
#define EXT0_ADVANCE_L 0
#define EXT0_ADVANCE_BACKLASH_STEPS 0
#define EXT0_WAIT_RETRACT_TEMP 150
#define EXT0_WAIT_RETRACT_UNITS 0
#define EXT0_SELECT_COMMANDS ""
#define EXT0_DESELECT_COMMANDS ""
#define EXT0_EXTRUDER_COOLER_PIN 11
#define EXT0_EXTRUDER_COOLER_SPEED 255
#define EXT0_DECOUPLE_TEST_PERIOD 12000
#define EXT0_JAM_PIN -1
#define EXT0_JAM_PULLUP 0
#define FEATURE_RETRACTION 1
#define AUTORETRACT_ENABLED 0
#define RETRACTION_LENGTH 2
#define RETRACTION_LONG_LENGTH 13
#define RETRACTION_SPEED 20
#define RETRACTION_Z_LIFT 0
#define RETRACTION_UNDO_EXTRA_LENGTH 0
#define RETRACTION_UNDO_EXTRA_LONG_LENGTH 0
#define RETRACTION_UNDO_SPEED 20
#define FILAMENTCHANGE_X_POS 0
#define FILAMENTCHANGE_Y_POS 0
#define FILAMENTCHANGE_Z_ADD  2
#define FILAMENTCHANGE_REHOME 1
#define FILAMENTCHANGE_SHORTRETRACT 5
#define FILAMENTCHANGE_LONGRETRACT 50
#define JAM_STEPS 220
#define JAM_SLOWDOWN_STEPS 320
#define JAM_SLOWDOWN_TO 70
#define JAM_ERROR_STEPS 500
#define JAM_MIN_STEPS 10
#define JAM_ACTION 1
#define RETRACT_DURING_HEATUP true
#define PID_CONTROL_RANGE 20
#define SKIP_M109_IF_WITHIN 2
#define SCALE_PID_TO_MAX 0
#define TEMP_HYSTERESIS 0
#define EXTRUDE_MAXLENGTH 160
#define NUM_TEMPS_USERTHERMISTOR0 0
#define USER_THERMISTORTABLE0 {}
#define NUM_TEMPS_USERTHERMISTOR1 0
#define USER_THERMISTORTABLE1 {}
#define NUM_TEMPS_USERTHERMISTOR2 0
#define USER_THERMISTORTABLE2 {}
#define GENERIC_THERM_VREF 5
#define GENERIC_THERM_NUM_ENTRIES 33
#define HEATER_PWM_SPEED 0
#define HAVE_HEATED_BED 0
#define HEATED_BED_MAX_TEMP 120
#define SKIP_M190_IF_WITHIN 3
#define HEATED_BED_SENSOR_TYPE 1
#define HEATED_BED_SENSOR_PIN TEMP_1_PIN
#define HEATED_BED_HEATER_PIN HEATER_1_PIN
#define HEATED_BED_SET_INTERVAL 5000
#define HEATED_BED_HEAT_MANAGER 0
#define HEATED_BED_PID_INTEGRAL_DRIVE_MAX 255
#define HEATED_BED_PID_INTEGRAL_DRIVE_MIN 80
#define HEATED_BED_PID_PGAIN_OR_DEAD_TIME   196
#define HEATED_BED_PID_IGAIN   33
#define HEATED_BED_PID_DGAIN 290
#define HEATED_BED_PID_MAX 255
#define HEATED_BED_DECOUPLE_TEST_PERIOD 300000
#define MIN_EXTRUDER_TEMP 150
#define MAXTEMP 275
#define MIN_DEFECT_TEMPERATURE -10
#define MAX_DEFECT_TEMPERATURE 290
#define ENDSTOP_PULLUP_X_MIN true
#define ENDSTOP_X_MIN_INVERTING true
#define MIN_HARDWARE_ENDSTOP_X true
#define ENDSTOP_PULLUP_Y_MIN true
#define ENDSTOP_Y_MIN_INVERTING true
#define MIN_HARDWARE_ENDSTOP_Y true
#define ENDSTOP_PULLUP_Z_MIN true
#define ENDSTOP_Z_MIN_INVERTING true
#define MIN_HARDWARE_ENDSTOP_Z true
#define ENDSTOP_PULLUP_X_MAX true
#define ENDSTOP_X_MAX_INVERTING false
#define MAX_HARDWARE_ENDSTOP_X false
#define ENDSTOP_PULLUP_Y_MAX true
#define ENDSTOP_Y_MAX_INVERTING false
#define MAX_HARDWARE_ENDSTOP_Y false
#define ENDSTOP_PULLUP_Z_MAX true
#define ENDSTOP_Z_MAX_INVERTING false
#define MAX_HARDWARE_ENDSTOP_Z false
#define max_software_endstop_r true
#define min_software_endstop_x false
#define min_software_endstop_y false
#define min_software_endstop_z false
#define max_software_endstop_x true
#define max_software_endstop_y true
#define max_software_endstop_z true
#define ENDSTOP_X_BACK_MOVE 5
#define ENDSTOP_Y_BACK_MOVE 5
#define ENDSTOP_Z_BACK_MOVE 2
#define ENDSTOP_X_RETEST_REDUCTION_FACTOR 3
#define ENDSTOP_Y_RETEST_REDUCTION_FACTOR 3
#define ENDSTOP_Z_RETEST_REDUCTION_FACTOR 3
#define ENDSTOP_X_BACK_ON_HOME 1
#define ENDSTOP_Y_BACK_ON_HOME 1
#define ENDSTOP_Z_BACK_ON_HOME 0
#define ALWAYS_CHECK_ENDSTOPS 1
#define X_ENABLE_ON 0
#define Y_ENABLE_ON 0
#define Z_ENABLE_ON 0
#define DISABLE_X 0
#define DISABLE_Y 0
#define DISABLE_Z 0
#define DISABLE_E 0
#define INVERT_X_DIR 1
#define INVERT_Y_DIR 0
#define INVERT_Z_DIR 0
#define X_HOME_DIR -1
#define Y_HOME_DIR -1
#define Z_HOME_DIR -1
#define X_MAX_LENGTH 110
#define Y_MAX_LENGTH 110
#define Z_MAX_LENGTH 110
#define X_MIN_POS 0
#define Y_MIN_POS 0
#define Z_MIN_POS 0
#define DISTORTION_CORRECTION 0
#define DISTORTION_CORRECTION_POINTS 5
#define DISTORTION_CORRECTION_R 100
#define DISTORTION_PERMANENT 1
#define DISTORTION_UPDATE_FREQUENCY 15
#define DISTORTION_START_DEGRADE 0.5
#define DISTORTION_END_HEIGHT 1
#define DISTORTION_EXTRAPOLATE_CORNERS 0
#define FEATURE_BABYSTEPPING 0
#define BABYSTEP_MULTIPLICATOR 1
#define DELTA_SEGMENTS_PER_SECOND_PRINT 180 // Move accurate setting for print moves
#define DELTA_SEGMENTS_PER_SECOND_MOVE 70 // Less accurate setting for other moves
#define DELTA_HOME_ON_POWER 0
#define DELTASEGMENTS_PER_PRINTLINE 24
#define STEPPER_INACTIVE_TIME 360L
#define MAX_INACTIVE_TIME 0L
#define MAX_FEEDRATE_X 200
#define MAX_FEEDRATE_Y 200
#define MAX_FEEDRATE_Z 20
#define HOMING_FEEDRATE_X 40
#define HOMING_FEEDRATE_Y 40
#define HOMING_FEEDRATE_Z 10
#define HOMING_ORDER HOME_ORDER_ZXY
#define ZHOME_MIN_TEMPERATURE 0
#define ZHOME_HEAT_ALL 1
#define ZHOME_HEAT_HEIGHT 20
#define ZHOME_X_POS 999999
#define ZHOME_Y_POS 999999
#define ENABLE_BACKLASH_COMPENSATION 0
#define X_BACKLASH 0
#define Y_BACKLASH 0
#define Z_BACKLASH 0
#define RAMP_ACCELERATION 1
#define STEPPER_HIGH_DELAY 2
#define DIRECTION_DELAY 0
#define STEP_DOUBLER_FREQUENCY 12000
#define ALLOW_QUADSTEPPING 1
#define DOUBLE_STEP_DELAY 1 // time in microseconds
#define MAX_ACCELERATION_UNITS_PER_SQ_SECOND_X 1000
#define MAX_ACCELERATION_UNITS_PER_SQ_SECOND_Y 1000
#define MAX_ACCELERATION_UNITS_PER_SQ_SECOND_Z 100
#define MAX_TRAVEL_ACCELERATION_UNITS_PER_SQ_SECOND_X 1000
#define MAX_TRAVEL_ACCELERATION_UNITS_PER_SQ_SECOND_Y 1000
#define MAX_TRAVEL_ACCELERATION_UNITS_PER_SQ_SECOND_Z 100
#define MAX_JERK 20
#define MAX_ZJERK 2
#define PRINTLINE_CACHE_SIZE 16
#define MOVE_CACHE_LOW 10
#define LOW_TICKS_PER_MOVE 250000
#define FEATURE_TWO_XSTEPPER 0
#define X2_STEP_PIN   ORIG_E1_STEP_PIN
#define X2_DIR_PIN    ORIG_E1_DIR_PIN
#define X2_ENABLE_PIN E1_ENABLE_PIN
#define FEATURE_TWO_YSTEPPER 0
#define Y2_STEP_PIN   ORIG_E1_STEP_PIN
#define Y2_DIR_PIN    ORIG_E1_DIR_PIN
#define Y2_ENABLE_PIN E1_ENABLE_PIN
#define FEATURE_TWO_ZSTEPPER 0
#define Z2_STEP_PIN   ORIG_E1_STEP_PIN
#define Z2_DIR_PIN    ORIG_E1_DIR_PIN
#define Z2_ENABLE_PIN E1_ENABLE_PIN
#define FEATURE_DITTO_PRINTING 0
#define USE_ADVANCE 0
#define ENABLE_QUADRATIC_ADVANCE 0
#define BAUDRATE 250000
#define ENABLE_POWER_ON_STARTUP 1
#define POWER_INVERTING 0
#define KILL_METHOD 1
#define ACK_WITH_LINENUMBER 1
#define WAITING_IDENTIFIER "wait"
#define ECHO_ON_EXECUTE 1
#define EEPROM_MODE 1
#define PS_ON_PIN 81
#define FEATURE_SERVO 0
#define SERVO0_PIN 11
#define SERVO1_PIN -1
#define SERVO2_PIN -1
#define SERVO3_PIN -1
#define SERVO0_NEUTRAL_POS  -1
#define SERVO1_NEUTRAL_POS  -1
#define SERVO2_NEUTRAL_POS  -1
#define SERVO3_NEUTRAL_POS  -1
#define UI_SERVO_CONTROL 0
#define FAN_KICKSTART_TIME  200
        #define FEATURE_WATCHDOG 1
#define FEATURE_Z_PROBE 0
#define Z_PROBE_BED_DISTANCE 10
#define Z_PROBE_PIN -1
#define Z_PROBE_PULLUP 0
#define Z_PROBE_ON_HIGH 0
#define Z_PROBE_X_OFFSET 0
#define Z_PROBE_Y_OFFSET 0
#define Z_PROBE_WAIT_BEFORE_TEST 0
#define Z_PROBE_SPEED 2
#define Z_PROBE_XY_SPEED 150
#define Z_PROBE_SWITCHING_DISTANCE 1
#define Z_PROBE_REPETITIONS 1
#define Z_PROBE_HEIGHT 40
#define Z_PROBE_START_SCRIPT ""
#define Z_PROBE_FINISHED_SCRIPT ""
#define FEATURE_AUTOLEVEL 1
#define Z_PROBE_X1 20
#define Z_PROBE_Y1 20
#define Z_PROBE_X2 160
#define Z_PROBE_Y2 20
#define Z_PROBE_X3 100
#define Z_PROBE_Y3 160
#define FEATURE_AXISCOMP 0
#define AXISCOMP_TANXY 0
#define AXISCOMP_TANYZ 0
#define AXISCOMP_TANXZ 0
#define SDSUPPORT 0
#define SDCARDDETECT -1
#define SDCARDDETECTINVERTED 0
#define SD_EXTENDED_DIR 1
#define SD_RUN_ON_STOP ""
#define SD_STOP_HEATER_AND_MOTORS_ON_STOP 1
#define ARC_SUPPORT 1
#define FEATURE_MEMORY_POSITION 1
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

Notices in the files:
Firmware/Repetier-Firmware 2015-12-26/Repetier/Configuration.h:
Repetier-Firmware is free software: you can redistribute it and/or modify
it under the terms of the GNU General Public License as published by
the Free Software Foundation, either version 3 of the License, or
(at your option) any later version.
